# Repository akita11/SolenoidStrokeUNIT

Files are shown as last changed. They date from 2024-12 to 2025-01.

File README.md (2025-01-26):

# SolenoidStokeUNIT

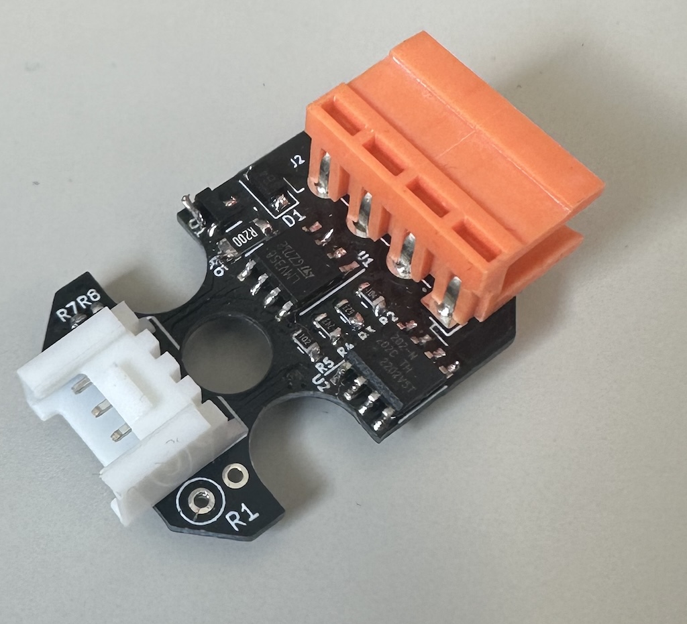
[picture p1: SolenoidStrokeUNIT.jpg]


ソレノイドのストローク位置によってインダクタンスが変化し、PWM制御時の電流波形が変化することを利用して、ソレノイドのPWM制御とストローク位置の計測（推定）を同時に行うための回路です。

**【注意：重要】**
実際の制御・計測の動作には、ソレノイドごとに特性の計測を行う必要があり、また特性の個体差、温度特性なども考慮する必要があります。そのため、**「これを使ってサンプルプログラムを書き込めば間違いなく動作する（制御ができる）」というものではなく、あくまでもこの原理検証の実験のための回路**ということをご理解ください。測定原理やサンプルプログラムは[こちら](https://github.com/akita11/SolenoidStrokeMeasureControl)に適宜まとめて更新していきます。

## 使い方

オレンジ色のコネクタ(VH3.96-4p)に、ソレノイド用の電源とソレノイドを接続します。M5Stackの[BAVGソケット](https://www.switch-science.com/products/7234)を使うと、電源は2.1mmプラグ、負荷はスプリング端子で接続できて便利です。

Grove端子にUART通信元（M5Stack等のマイコンやUSBシリアル変換器）を接続し、本UNITに対してコマンド送信や結果の受信を行います。Grove端子の信号は、"RXD(受信) / TXD(送信) / VDD(+5V) / GND"の順です。ここでRXDとTXDの「主語」は本UNITです。つまり本UNITの"RXD"は、UART送信元の送信(TX)に接続します。（なおM5StackのPortCのTX/RXはこの順序ですのでそのまま接続できます）

### コマンド

コマンドは、基本的に、「コマンドを表す1文字 + 引数（10進数表記：ないものもある） + <CR> or <LF>」の形式です。各コマンドの成功時には'S'と'P'以外では指定された設定が返され、定義されていないコマンドでは'?'が返されます。

- 'S' : 測定開始（引数なし）：後述の形式で測定データが送出されます
- 'P' : 測定停止（引数なし）
- 'D' : PWM ON時間の設定（引数：PWM ON時間（単位は0.8us））
- 'T' : PWM ON時間の設定（引数：PWM周期（単位は0.8us））
- '0' : PWM ONから第1サンプリング点までの時間（引数：PWM周期（単位は0.8us））
- '1' : PWM ONから第2サンプリング点までの時間（引数：PWM周期（単位は0.8us））
- 'C' : 内部蓄積回数（引数：回）

### 送出データの形式

AAAABBBB + <CR> + <LF>

- AAAA : 第1サンプリング点の電圧値（10進数4桁）：0=0V, 1023=5V
- BBBB : 第2サンプリング点の電圧値（10進数4桁）：0=0V, 1023=5V

### 増幅率の調整

ソレノイドの駆動電流を0.2Ωの抵抗で電圧変換し、それをオペアンプ（非反転増幅回路）で増幅して"ADC"端子に出力しています。その増幅率は、用いるソレノイド・電源電圧からきまる駆動電流にあわせて、適切な範囲に調整する必要があります。"ADC"端子の波形をオシロ等で計測し、用いるマイコンのADCの入力電圧範囲に収まるように増幅率を調整します。増幅率は基板裏面のハンダジャンパJP3/JP4JP5で調整できます。（JP3は初期状態でONになっていますので、OFFにする場合はパターンをカットしてください）

- JP3/JP4/JP5=ON/OFF/OFF : 101倍
- JP3/JP4/JP5=ON/ON/OFF : 39倍
- JP3/JP4/JP5=ON/OFF/ON : 20倍
- JP3/JP4/JP5=ON/ON/ON : 16倍
- JP3/JP4/JP5=OFF/OFF/OFF : R1にとりつける抵抗から決まる倍率（(R1÷1[kΩ]+1)倍）

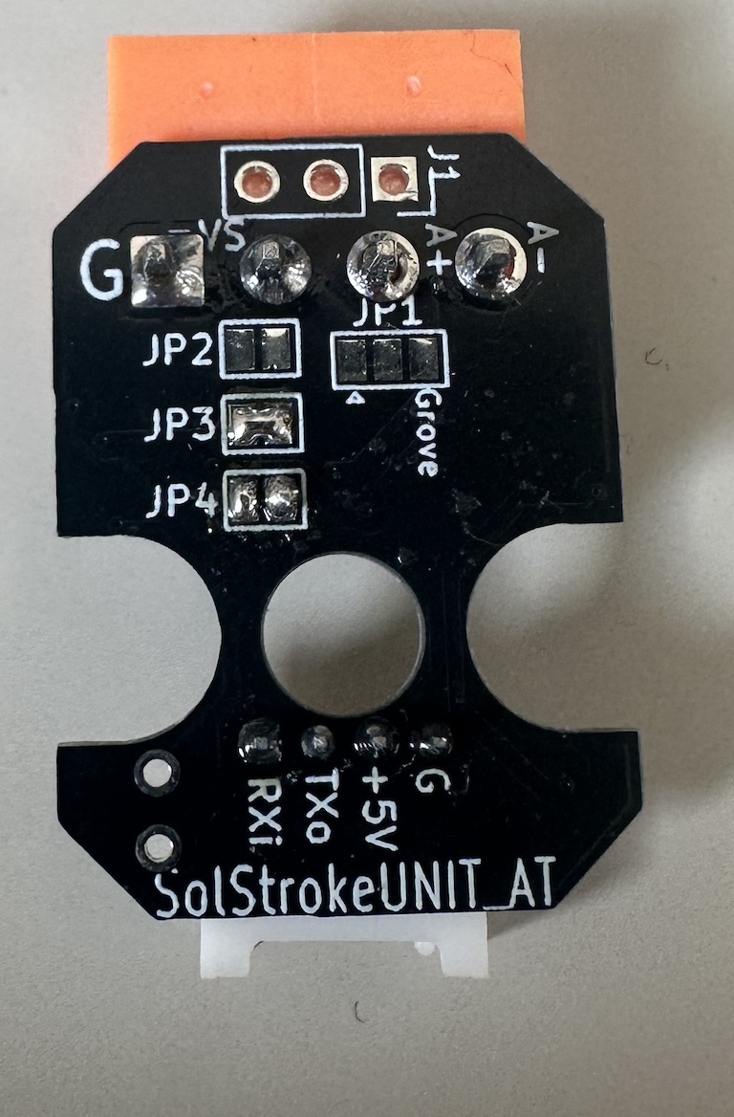
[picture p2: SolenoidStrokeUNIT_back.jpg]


## 測定原理

ソレノイドは電気回路的にはインダクタで、そのインダクタンスはストローク（プランジャ）位置で変化します。そのためON時の充電電流の波形は、ストローク位置で変化します。ただし充電開始時の電流はOFF期間中の放電特性できまるため、ゼロからとは限りません。またPWMのON時間（PWMのデューティー比）によっても波形は変化します。

ソレノイドによっては、ON後の2箇所の時点（例えば100us後と700us後）での電流の差が、PWMのON時間（PWMのデューティー比）ごとにストローク位置に伴って変化するため、与えているPWM ON時間とその電流差から、ストローク位置を計測（推定）することができます。具体的には、PWM ON後に電流が徐々に増加するところの2点（第1・第2サンプリング点）の電圧から、あらかじめ学習させた深層学習CNNモデルによってソレノイドのストローク位置とコイル温度を求めることができます。詳細はarXivの[論文(1)](https://arxiv.org/abs/2405.11721)と[論文(2)](https://arxiv.org/abs/2411.07270)にまとめてあります。

ただしソレノイドによっては、この電流差がストロークによってほとんど変化しないため、この方法では位置を計測することができません。そのため、複数点の電流の計測値から、予め計測した位置と電流値との差（の総和）が最小となるように反復計算で位置を求めるアルゴリズムを開発中です。まだ安定性や精度の検証は不十分ですが、参考用に上記GitHubにいくつかのソレノイドのCNNモデルと、それをESP32(M5Stack等)で実行するためのソースコードをおいてあります。

現在、SSBH-0830-02用の推定モデルとそれを使った位置制御(Control_ESP32/)をおいてあります。上記GitHubの生活をREADME.mdは別の計測制御(SolenoidStokeMeasureControlUNIT)用の情報が書いてありますが、この位置制御のソースコードは、本ユニット用のものです。

## Author

Junichi Akita (akita@ifdl.jp, @akita11)

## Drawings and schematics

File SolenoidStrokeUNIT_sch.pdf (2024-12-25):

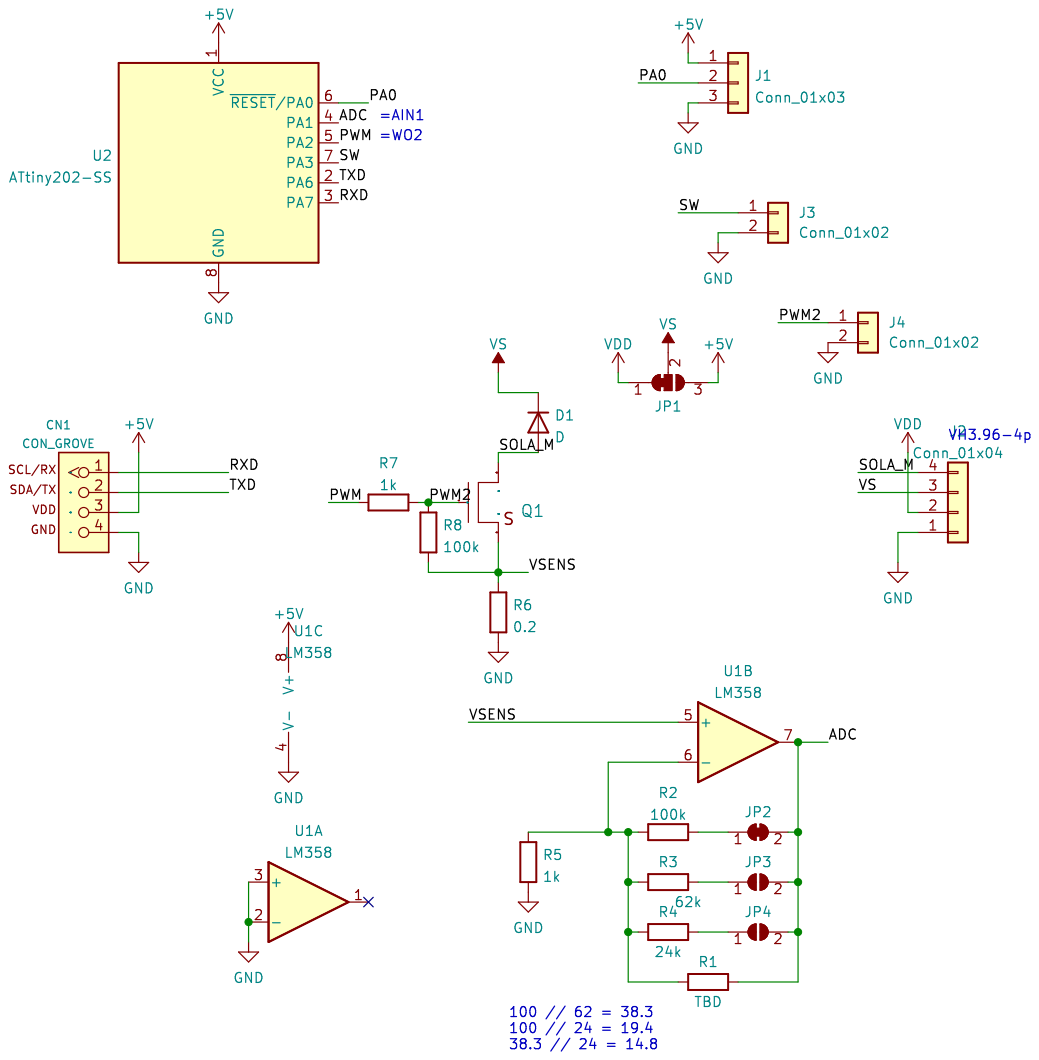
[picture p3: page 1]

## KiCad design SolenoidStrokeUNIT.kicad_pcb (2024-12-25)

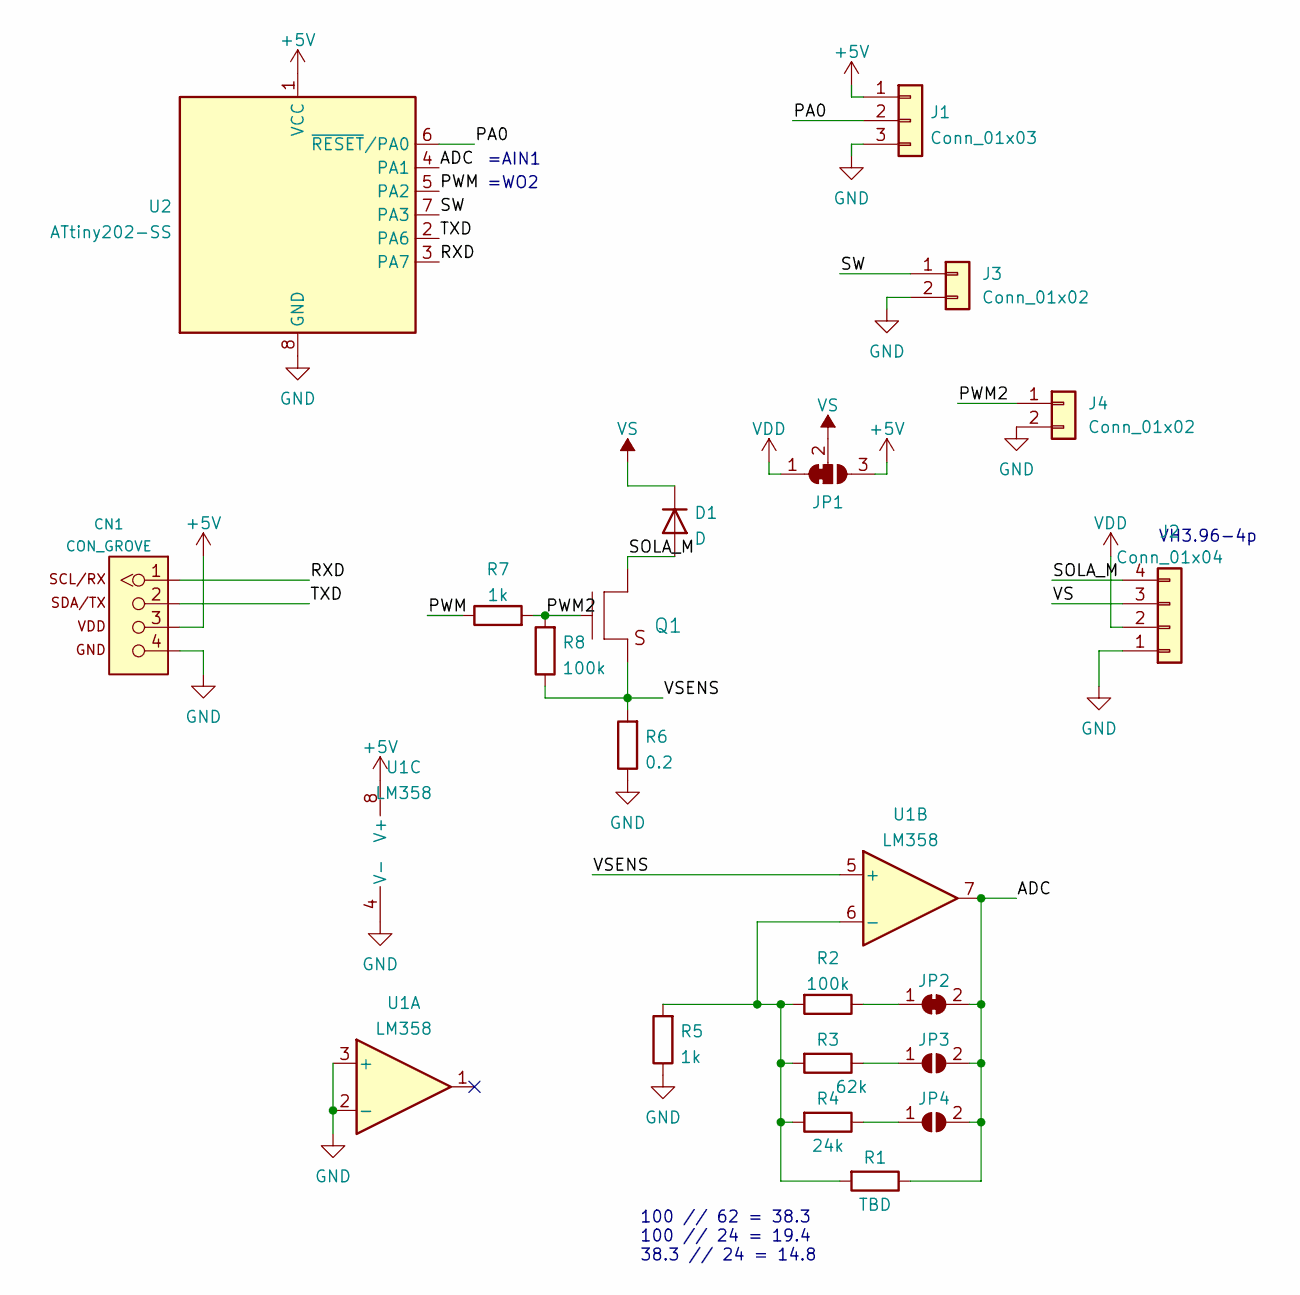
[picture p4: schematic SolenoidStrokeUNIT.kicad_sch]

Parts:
CN1: CON_GROVE; CON_GROVE_H
D1: D; D_SOD-123F
J1: Conn_01x03; PinSocket_1x03_P2.54mm_Vertical
J2: Conn_01x04; JST_VH_S4P-VH_1x04_P3.96mm_Horizontal
J3, J4: Conn_01x02; PinSocket_1x02_P2.54mm_Vertical
JP1: SolderJumper_3_Bridged12; SolderJumper-3_P1.3mm_Bridged2Bar12_Pad1.0x1.5mm
JP2: SolderJumper_2_Bridged; SolderJumper-2_P1.3mm_Bridged_Pad1.0x1.5mm
JP3, JP4: SolderJumper_2_Open; SolderJumper-2_P1.3mm_Open_Pad1.0x1.5mm
Q1: TR_NMOS_IRLML6344; SOT-23
R1: TBD; R_Axial_DIN0207_L6.3mm_D2.5mm_P2.54mm_Vertical
R2, R8: 100k; R_0603_1608Metric
R3: 62k; R_0603_1608Metric
R4: 24k; R_0603_1608Metric
R5, R7: 1k; R_0603_1608Metric
R6: 0.2; R_1206_3216Metric
U1: LM358; SO-8_3.9x4.9mm_P1.27mm
U2: ATtiny202-SS; SOIC-8_3.9x4.9mm_P1.27mm

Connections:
+5V: CN1.3, J1.1, JP1.3 (B), U1.8 (V+), U2.1 (VCC)
/ADC: JP2.2 (B), JP3.2 (B), JP4.2 (B), R1.1, U1.7, U2.4 (PA1)
/PA0: J1.2, U2.6 (~RESET/PA0)
/PWM: R7.1, U2.5 (PA2)
/PWM2: J4.1, Q1.1 (G), R7.2, R8.2
/RXD: CN1.1, U2.3 (PA7)
/SOLA_M: D1.2 (A), J2.4, Q1.3 (D)
/SW: J3.1, U2.7 (PA3)
/TXD: CN1.2, U2.2 (PA6)
/VSENS: Q1.2 (S), R6.2, R8.1, U1.5 (+)
GND: CN1.4, J1.3, J2.1, J3.2, J4.2, R5.1, R6.1, U1.2 (-), U1.3 (+), U1.4 (V-), U2.8 (GND)
unnamed: JP2.1 (A), R2.1
unnamed: JP3.1 (A), R3.1
unnamed: JP4.1 (A), R4.1
unnamed: R1.2, R2.2, R3.2, R4.2, R5.2, U1.6 (-)
VDD: J2.2, JP1.1 (A)
VS: D1.1 (K), J2.3, JP1.2 (C)

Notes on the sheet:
100 // 62 = 38.3 100 // 24 = 19.4 38.3 // 24 = 14.8
=WO2
VH3.96-4p
=AIN1

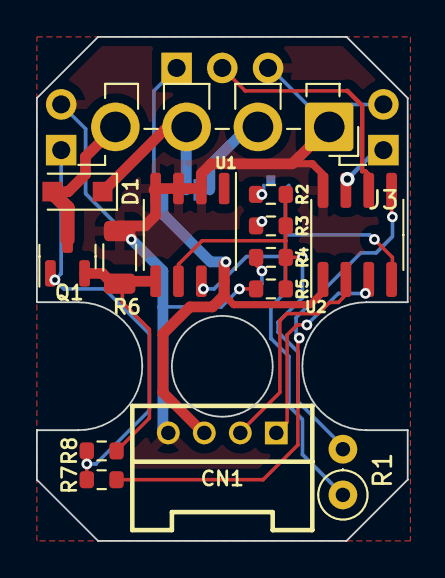
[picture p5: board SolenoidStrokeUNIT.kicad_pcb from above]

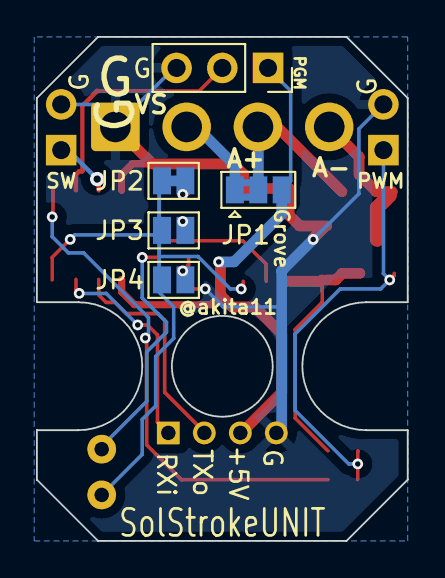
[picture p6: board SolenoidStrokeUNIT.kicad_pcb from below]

Board: 2 copper layers, 20.6 x 28.0 mm, 21 parts (5 on the bottom side), 17 nets.
